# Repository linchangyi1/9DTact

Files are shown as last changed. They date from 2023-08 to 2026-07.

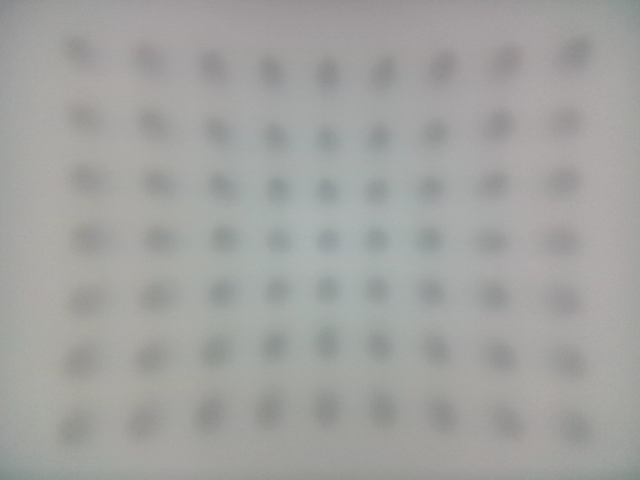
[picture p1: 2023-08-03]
shape_reconstruction/calibration/sensor_1/camera_calibration/sample.png

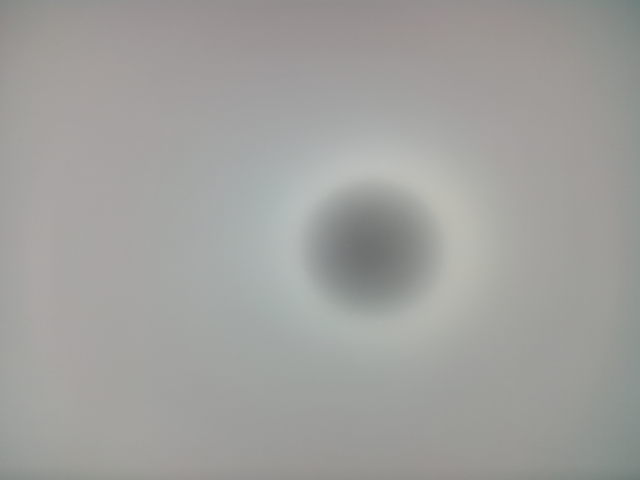
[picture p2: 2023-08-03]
shape_reconstruction/calibration/sensor_2/depth_calibration/sample.png

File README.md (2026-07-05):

# 9DTact
### Feel free to use this open-source project for commercial purposes!

# Table of contents
1. [Overview](#overview)
2. [Installation](#installation)
3. [3D Shape Reconstruction](#reconstruction)
   1. [Camera Calibration](#camera_calibration)
   2. [Sensor Calibration](#sensor_calibration)
   3. [Shape Reconstruction](#shape_reconstruction)
4. [6D Force Estimation](#estimation)
   1. [BOTA Driver](#bota)
   2. [Data Collection](#collection)
   3. [Data Processing](#processing)
   4. [Model Training](#training)
   5. [Force Estimation](#inference)
5. [Run in ROS](#ros)
   1. [Shape Reconstruction in ROS](#shape_ros)
   2. [Force Estimation in ROS](#force_ros)
   3. [Simultaneous Shape Reconstruction and Force Estimation (SSAF) in ROS](#shape_force)
6. [DTact Series Papers](#papers)

## Overview 
**This repository contains the code and the hardware source files for the paper:**



<b>9DTact: A Compact Vision-Based Tactile Sensor for Accurate 3D Shape Reconstruction and Generalizable 6D Force Estimation</b> <br>
[Changyi Lin](https://linchangyi1.github.io/),
[Han Zhang](https://doublehan07.github.io/),
Jikai Xu, Lei Wu, and
[Huazhe Xu](http://hxu.rocks/) <br>
RAL, 2023 <br>
[Website](https://linchangyi1.github.io/9DTact/) /
[Arxiv Paper](https://arxiv.org/abs/2308.14277) /
[Video Tutorial](https://www.youtube.com/watch?v=-oRtW398JDY) /
[Bom (CN)](https://docs.google.com/document/d/1d8c0Pbj_9otzWVxE94c6c-DW61ETBbJZIjVFKe4_OXI/edit?usp=sharing) /
[Production](https://e.tb.cn/h.hJlaI3aoyO30DGk?tk=K9Vm4iYdHwj)

## Installation 
#### Create a conda environment:
```bash
conda create -n 9dtact python=3.8
```
#### Install pytorch (choose the version that is compatible with your computer):
```bash
conda activate 9dtact
conda install pytorch torchvision torchaudio pytorch-cuda=11.8 -c pytorch -c nvidia
```
#### In this repository, install the other requirements:
```bash
pip install -e .
```

## 3D Shape Reconstruction 
For all the terminals used in this section, they are located in the **shape_reconstruction** directory and based on the **9dtact** conda environment:
```bash
cd shape_reconstruction
conda activate 9dtact
```

If you are using the **production** version of 9DTact, you do **not** need to calibrate the camera and sensor.
Please proceed directly to Step 3 (Shape Reconstruction).

### 1. Camera Calibration 
Before getting started, **adjust the camera focus** by rotating the lens until objects approximately 15 mm away appear clear.

Then, 3d print the [calibration board](9DTact_Design/fabrication/calibration_board.STL).<br>
Run:
```bash
python _1_Camera_Calibration.py
```
Just follow the printed instructions.

### 2. Sensor Calibration 
Firstly, prepare a ball with a radius of 4.0 mm.
(The radius of the ball depends on the thickness of the sensor surface.
4.0 mm is just a recommendation.)<br>
Then, run:
```bash
python _2_Sensor_Calibration.py
```
Just follow the printed instructions.

### 3. Shape Reconstruction 
```bash
python _3_Shape_Reconstruction.py
```
Press 'y' when the tactile image is stably captured, which will served as the reference image.

## 6D Force Estimation 
### 1. BOTA Driver 
**If you want to collect force data with a BOTA MiniONE Pro sensor, you need to:**<br>
Create a directory named 'bota_ws' as the ROS workspace, and install the [bota driver package](https://gitlab.com/botasys/bota_driver).

### 2. Data Collection 
#### At the first terminal, open the BOTA sensor:
```bash
cd ~/xxx/bota_ws # Modify 'xxx' to enter the workspace directory
source devel/setup.bash
roslaunch rokubimini_serial rokubimini_serial.launch
```
#### At the second terminal, run:
```bash
source ~/xxx/bota_ws/devel/setup.bash
cd data_collection
conda activate 9dtact
python collect_data.py
```
#### At the third terminal, open the 9DTact sensor:
```bash
cd shape-force-ros
conda activate 9dtact
python _1_Sensor_ros.py
```

### 3. Data Processing 
#### Open a terminal, normalize the wrench:
```bash
cd data_collection
conda activate 9dtact
python wrench_normalization.py  # remember to modify the object_num
```
#### At the same terminal, split the data by running:
```bash
python split_train_test.py
```
and also:
```bash
python split_train_test(objects).py
```

### 4. Model Training 
To train the model on the stadard training dataset, run:
```bash
cd force_estimation
python train.py --model_name="Densenet" --model_layer=169 --optimizer="ADAM" --lrs=False --image_type="RGB" --cuda_index=6 --resize_img=False --train_mode=True --test_object=False --mixed_image=True --pretrained=False --batch_size=64 --num_epoch=200 --learning_rate=5.0e-4 --weight_decay=0.0
```
You may also choose to use [Weights and Bias (wandb)](https://docs.wandb.ai/quickstart) by setting use_wandb as True,
which helps to track the training performance.

### 5. Force Estimation 
You need to specify a model saved in the 'saved_models' directory as an estimator,
by modifying the 'weights' parameters in the [force_config.yaml](force_estimation/force_config.yaml).<br>
After that, run:
```bash
cd force_estimation
python _1_Force_Estimation.py
```

## Run in ROS 
### 1. Shape Reconstruction in ROS 
#### At the first terminal, open the 9DTact sensor:
```bash
cd shape-force_ros
conda activate 9dtact
python _1_Sensor_ros.py
```
#### At the second terminal, run:
```bash
cd shape-force_ros
conda activate 9dtact
python _2_Shape_Reconstruction_ros.py
```

### 2. Force Estimation in ROS 
#### At the first terminal, open the 9DTact sensor:
```bash
cd shape-force_ros
conda activate 9dtact
python _1_Sensor_ros.py
```
#### At the second terminal, run:
```bash
cd shape-force_ros
conda activate 9dtact
python _3_Force_Estimation_ros.py
```
#### (Optional for visualization) At the third terminal, open the visualization window:
```bash
cd force_estimation
conda activate 9dtact
python force_visualizer.py
```
### 3. Simultaneous Shape Reconstruction and Force Estimation (SSAF) in ROS 
#### At the first terminal, open the force estimator:
```bash
cd shape-force_ros
conda activate 9dtact
python _3_Force_Estimation_ros.py
```
#### At the second terminal, run:
```bash
cd shape-force_ros
conda activate 9dtact
python _4_Shape_Force_ros.py
```
## DTact Series Papers 
- [DTact: A Vision-Based Tactile Sensor that Measures High-Resolution 3D Geometry Directly from Darkness](https://arxiv.org/abs/2209.13916), Lin et al., ICRA 2023
- [9DTact: A Compact Vision-Based Tactile Sensor for Accurate 3D Shape Reconstruction and Generalizable 6D Force Estimation](https://arxiv.org/abs/2308.14277), Lin et al., RAL 2023
- [Design and Evaluation of a Rapid Monolithic Manufacturing Technique for a Novel Vision-Based Tactile Sensor: C-Sight](https://www.mdpi.com/1424-8220/24/14/4603), Fan et al., MDPI Sensors 2024
- [DTactive: A Vision-Based Tactile Sensor with Active Surface](https://arxiv.org/abs/2410.08337), Xu et al., IROS 2025
- [VET: A Visual-Electronic Tactile System for Immersive Human-Machine Interaction](https://arxiv.org/pdf/2503.23440), Zhang et al., arxiv 2025
- [PP-Tac: Paper Picking Using Tactile Feedback in Dexterous Robotic Hands](https://arxiv.org/abs/2504.16649), Lin et al., RSS 2025
- [AllTact Fin Ray: A Compliant Robot Gripper with Omni-Directional Tactile Sensing](https://arxiv.org/pdf/2504.18064), Liang et al., arxiv 2025
- [SuperMag: Vision-based Tactile Data Guided High-resolution Tactile Shape Reconstruction for Magnetic Tactile Sensors](https://arxiv.org/pdf/2507.20002), Hou et al., IROS 2025
- [UTact: Underwater Vision-Based Tactile Sensor with Geometry Reconstruction and Contact Force Estimation](https://advanced.onlinelibrary.wiley.com/doi/pdfdirect/10.1002/adrr.202500091), Zhang et al., Advanced Robotics Research 2025
- [exUMI: Extensible Robot Teaching System with Action-aware Task-agnostic Tactile Representation](https://openreview.net/attachment?id=b86nyIOJWq&name=pdf), Xu et al., CoRL 2025
- [TacScope: A Miniaturized Vision-Based Tactile Sensor for Surgical Applications](https://advanced.onlinelibrary.wiley.com/doi/10.1002/adrr.202500117), Prince et al., Advanced Robotics Research 2025
- [Design and application of multimodal visual-tactile sensor for object information perception](https://www.sciencedirect.com/science/article/pii/S0924424726000804?via%3Dihub), Wang et al., Sensors and Actuators 2026
- [A Low-Cost Vision-Based Tactile Gripper with Pretraining Learning for Contact-Rich Manipulation](https://arxiv.org/pdf/2602.00514), Liu et al., arxiv 2026
- [SpikingTac: A Miniaturized Neuromorphic Visuotactile Sensor for High-Precision Dynamic Tactile Imprint Tracking](https://arxiv.org/pdf/2602.23654), Jiang et al., arxiv 2026
- [Heterogeneous Tactile Transformer](https://arxiv.org/pdf/2606.29948), Bi et al., arxiv 2026

## Reference
```
@inproceedings{lin2023dtact,
  title={Dtact: A vision-based tactile sensor that measures high-resolution 3d geometry directly from darkness},
  author={Lin, Changyi and Lin, Ziqi and Wang, Shaoxiong and Xu, Huazhe},
  booktitle={2023 IEEE International Conference on Robotics and Automation (ICRA)},
  pages={10359--10366},
  year={2023},
  organization={IEEE}
}
```
```
@article{lin20239dtact,
  title={9dtact: A compact vision-based tactile sensor for accurate 3d shape reconstruction and generalizable 6d force estimation},
  author={Lin, Changyi and Zhang, Han and Xu, Jikai and Wu, Lei and Xu, Huazhe},
  journal={IEEE Robotics and Automation Letters},
  volume={9},
  number={2},
  pages={923--930},
  year={2023},
  publisher={IEEE}
}
```

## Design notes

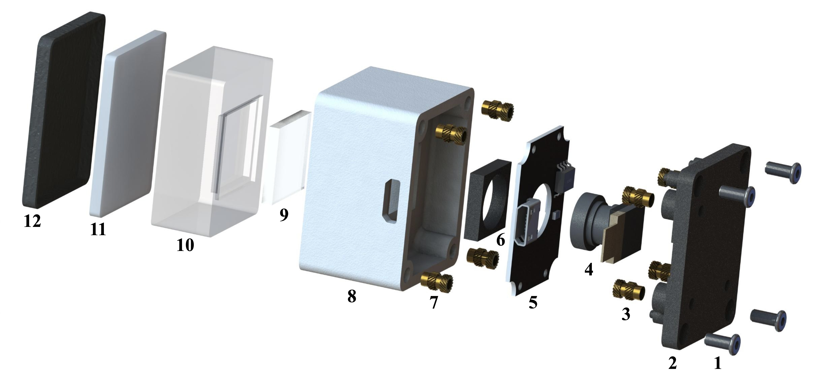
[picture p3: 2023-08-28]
source/design.jpeg

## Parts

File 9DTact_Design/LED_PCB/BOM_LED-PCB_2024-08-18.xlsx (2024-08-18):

No. | Quantity | Comment | Designator | Footprint | Value | Manufacturer Part | Manufacturer | Supplier Part | Supplier
1 | 8 | BZ-S2835BW9C1-02-3V-UV | LED1,LED2,LED3,LED4,LED5,LED6,LED7,LED8 | LED-SMD_L3.5-W2.8-FD-2835_WHITE |  | BZ-S2835BW9C1-02-3V-UV | baizou(百洲） | C2833052 | LCSC
2 | 1 | 20kΩ | R1 | R0805 | 20kΩ | RT0805CRE0720KL | YAGEO(国巨) | C706298 | LCSC
3 | 1 | CN5711 | U1 | SOIC-8_L5.0-W4.0-P1.27-LS6.0-BL-EP2.0 |  | CN5711 | CONSONANCE(上海如韵) | C35634 | LCSC
4 | 1 | MICRO-02-G4P1-A1T2 | USB3 | MICRO-USB-SMD_MICRO-02-GXPX-A1T2 |  | MICRO-02-G4P1-A1T2 | Yuandi(台湾元迪) | C2682525 | LCSC

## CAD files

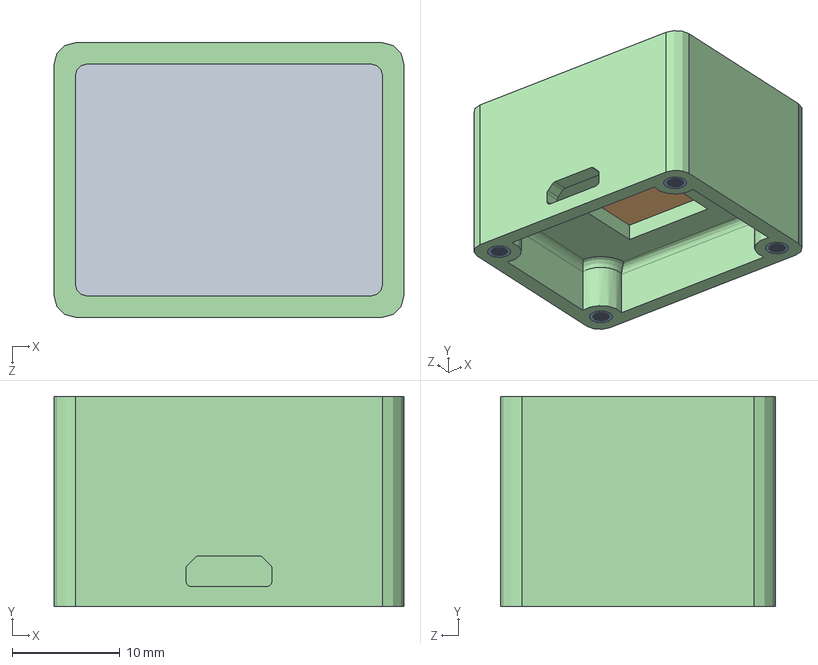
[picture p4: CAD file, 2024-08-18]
9DTact_Design/2_Diffusion_Module/2_Diffusion_Module.SLDASM
32.5 x 19.5 x 25.5 mm
sensor_shell
nut(2-3-5) x 4
acrylic_window
transparent_gel

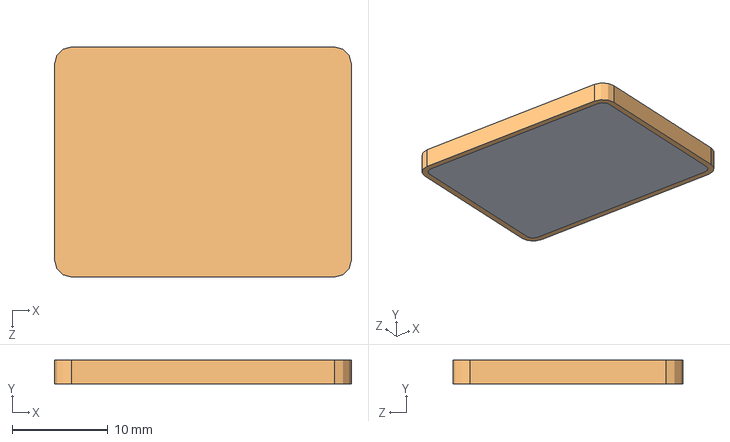
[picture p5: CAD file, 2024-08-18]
9DTact_Design/3_Contact_Module/3_Contact_Module.SLDASM
31.1 x 2.50 x 24.1 mm
translucent_gel
black_gel

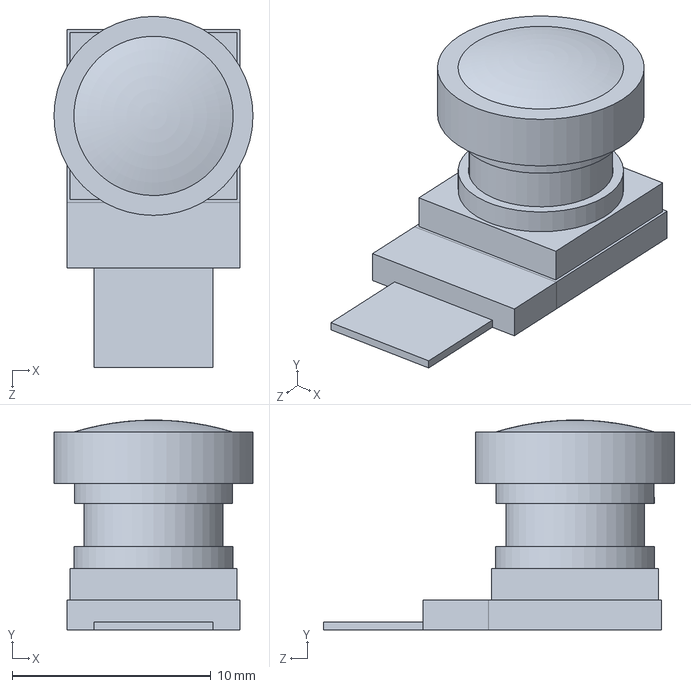
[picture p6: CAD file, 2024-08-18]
9DTact_Design/1_Perception_Module/camera(frank-s15-v1.0).SLDPRT
10.0 x 10.6 x 17.6 mm

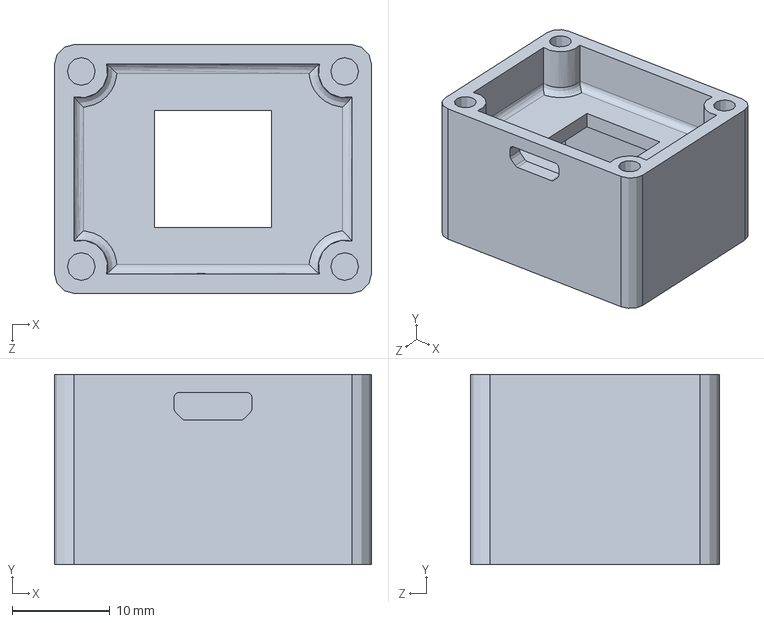
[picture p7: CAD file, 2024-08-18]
9DTact_Design/2_Diffusion_Module/sensor_shell.SLDPRT
32.5 x 19.5 x 25.5 mm

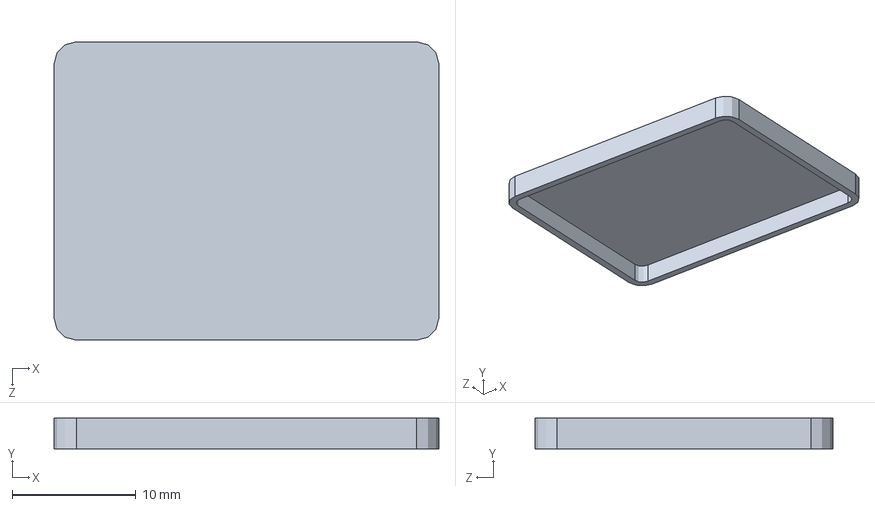
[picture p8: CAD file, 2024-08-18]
9DTact_Design/3_Contact_Module/black_gel.SLDPRT
31.1 x 2.50 x 24.1 mm

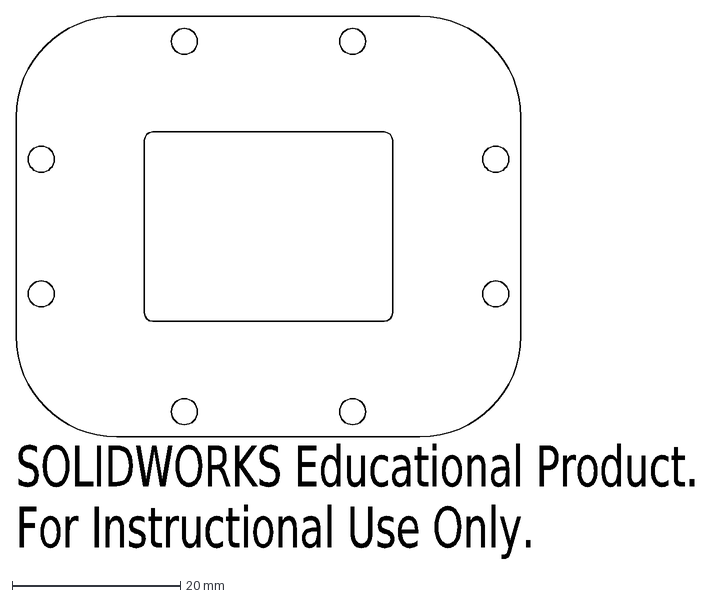
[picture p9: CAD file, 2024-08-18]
9DTact_Design/fabrication/mold_1_thickness_2.5mm.DXF
SOLIDWORKS Educational Product.
For Instructional Use Only.

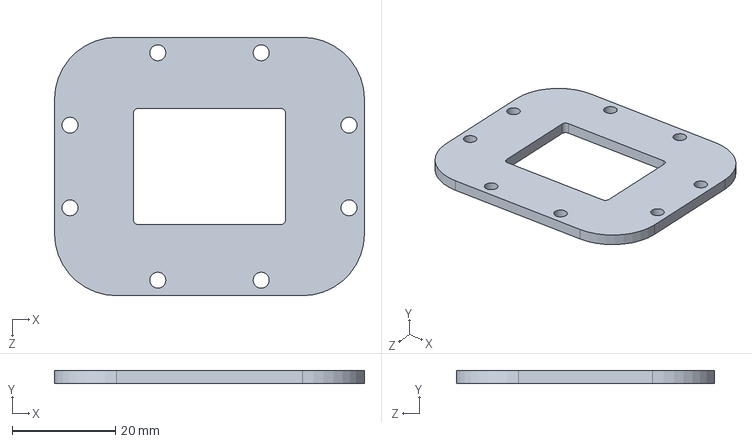
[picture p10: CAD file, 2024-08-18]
9DTact_Design/mold/mold_1.SLDPRT
60.0 x 2.50 x 50.0 mm

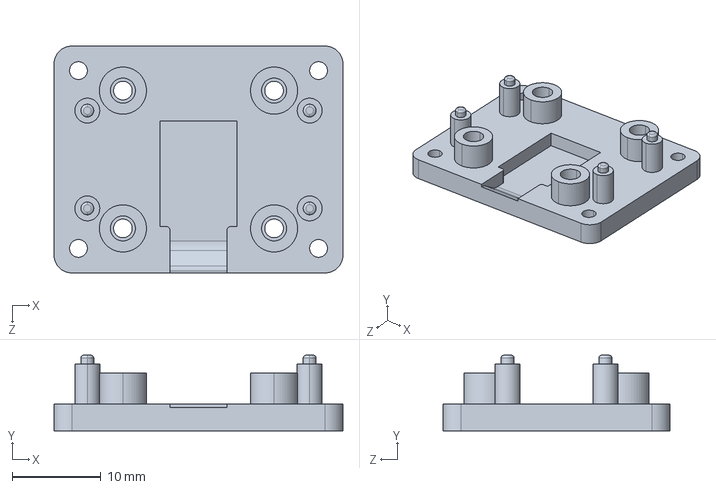
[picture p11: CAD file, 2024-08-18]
9DTact_Design/fabrication/sensor_base.STEP
32.5 x 8.50 x 25.5 mm

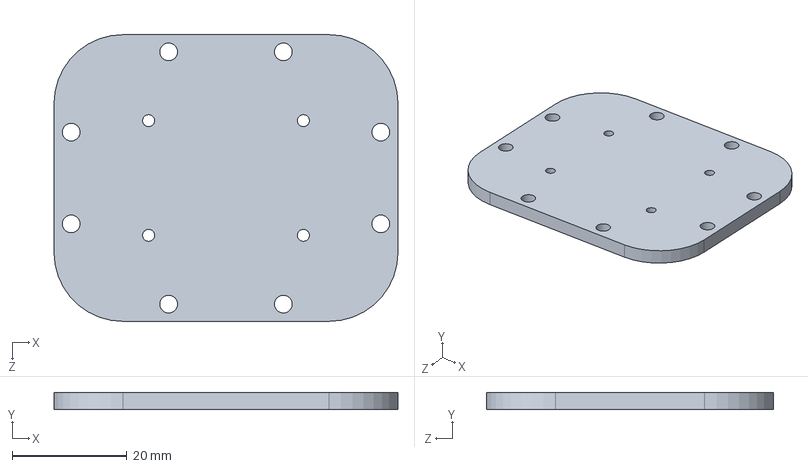
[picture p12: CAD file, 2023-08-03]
9DTact_Design/mold/mold_base.SLDPRT
60.0 x 3.00 x 50.0 mm

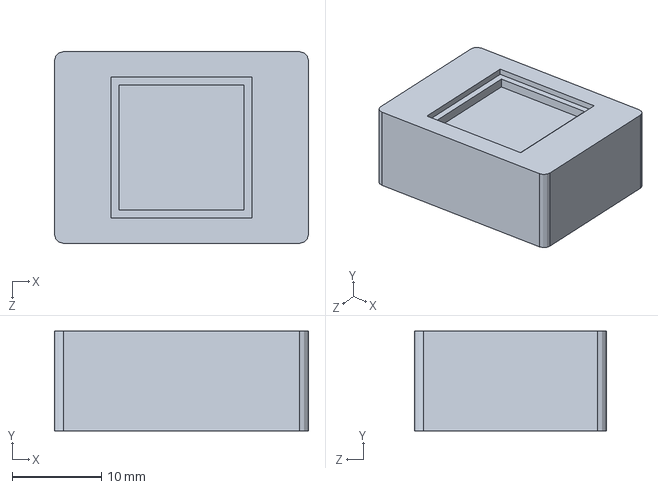
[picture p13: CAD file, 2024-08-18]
9DTact_Design/2_Diffusion_Module/transparent_gel.SLDPRT
28.5 x 11.2 x 21.5 mm

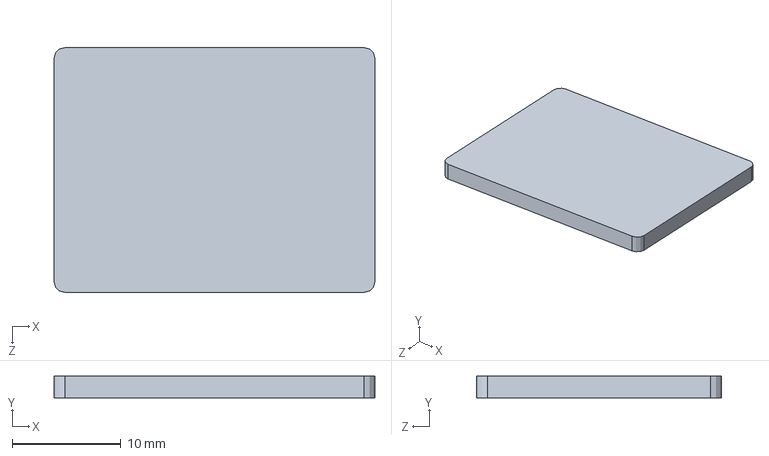
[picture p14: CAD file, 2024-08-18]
9DTact_Design/3_Contact_Module/translucent_gel.SLDPRT
29.5 x 2.00 x 22.5 mm

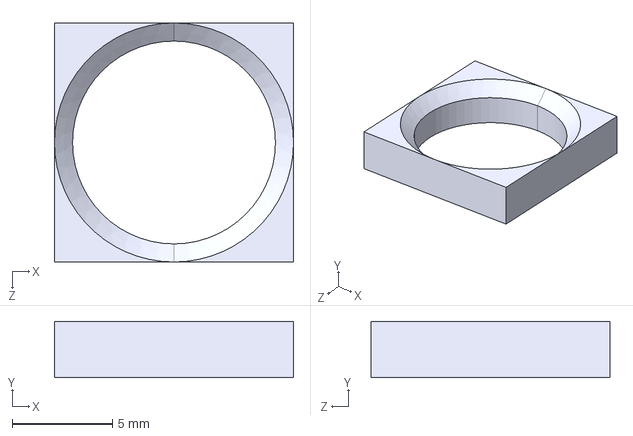
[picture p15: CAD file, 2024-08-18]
9DTact_Design/fabrication/isolation_ring.STEP
11.9 x 2.80 x 11.9 mm

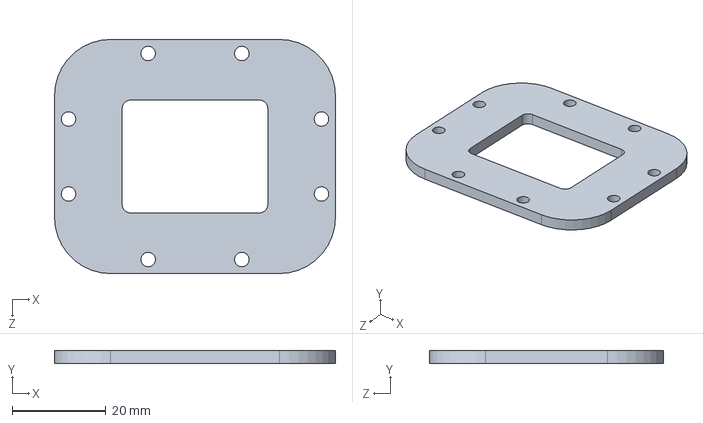
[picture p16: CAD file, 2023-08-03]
9DTact_Design/mold/mold_2.SLDPRT
60.0 x 2.80 x 50.0 mm

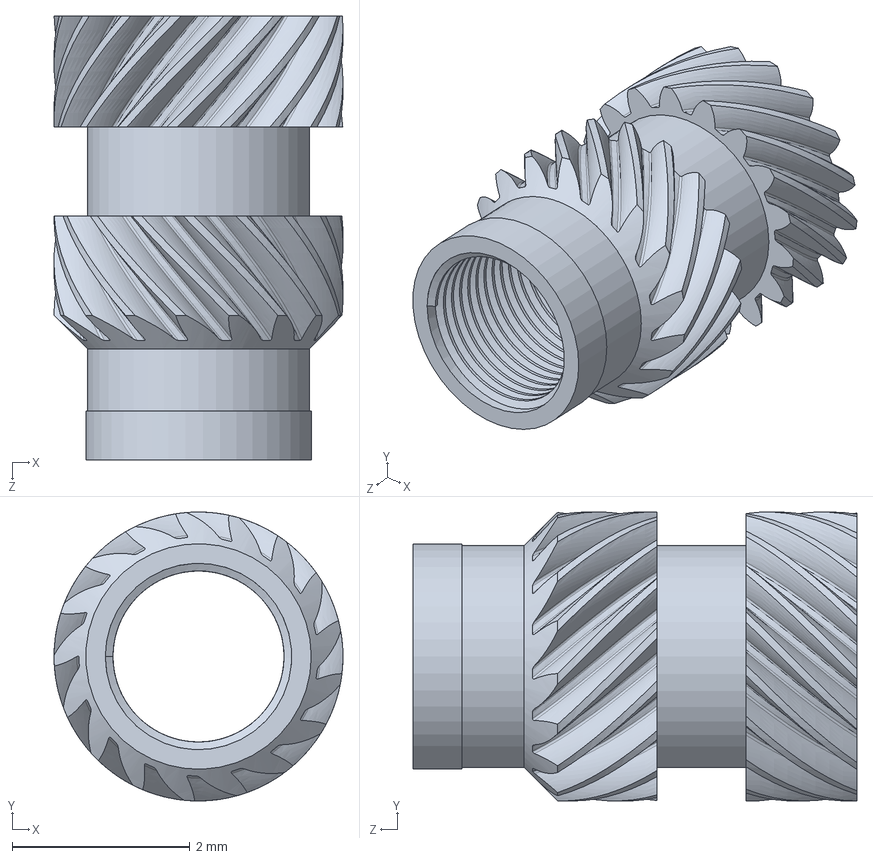
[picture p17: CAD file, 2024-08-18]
9DTact_Design/1_Perception_Module/nut(2-3-5).SLDPRT
3.26 x 3.25 x 5.00 mm

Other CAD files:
9DTact_Design/LED_PCB/LED_Model_from_JLC/led_board_combined.SLDASM
9DTact_Design/1_Perception_Module/sensor_base.SLDPRT
9DTact_Design/2_Diffusion_Module/acrylic_window.SLDPRT
9DTact_Design/fabrication/sensor_shell.STEP
9DTact_Design/1_Perception_Module/screw(M2-5).SLDPRT
9DTact_Design/2_Diffusion_Module/isolation_ring.SLDPRT
9DTact_Design/fabrication/calibration_board.SLDPRT
9DTact_Design/fabrication/calibration_board.STEP
9DTact_Design/fabrication/calibration_board.STL
9DTact_Design/fabrication/isolation_ring.STL
9DTact_Design/fabrication/mold_2_thickness_2.8mm.DXF
9DTact_Design/fabrication/mold_base_thickness_3.0mm.DXF
9DTact_Design/fabrication/sensor_base.STL
9DTact_Design/fabrication/sensor_shell.STL

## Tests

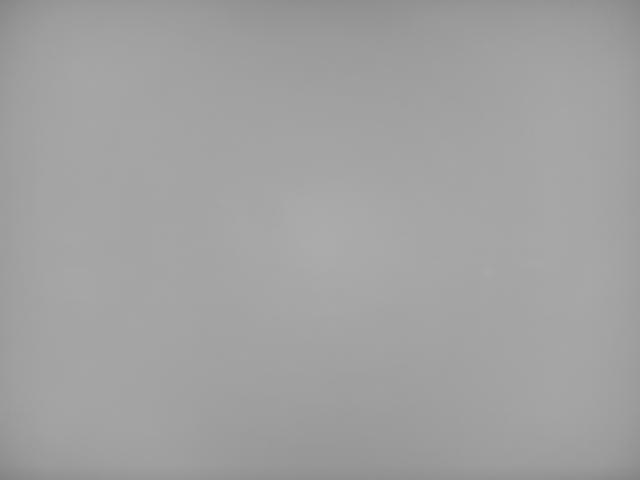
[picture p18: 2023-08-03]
shape_reconstruction/calibration/sensor_1/camera_calibration/ref_GRAY.png

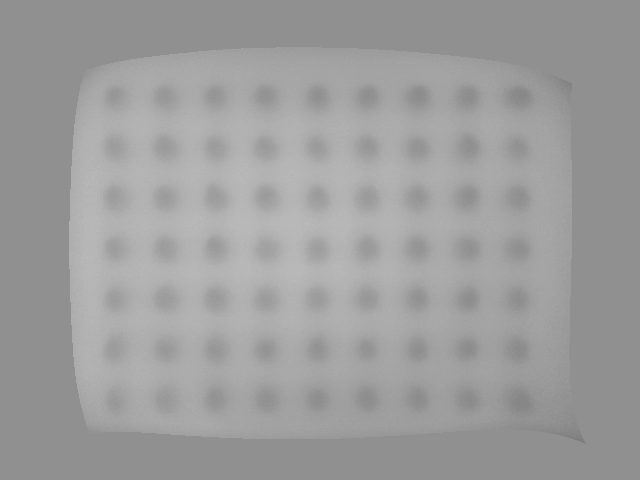
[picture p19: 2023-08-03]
shape_reconstruction/calibration/sensor_2/camera_calibration/sample_new.png

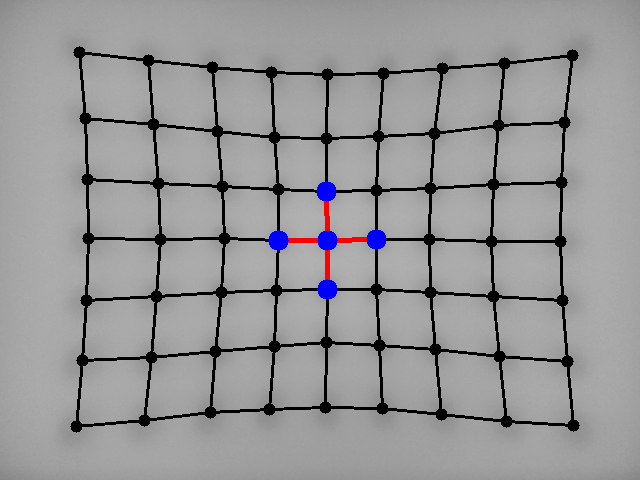
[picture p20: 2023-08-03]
shape_reconstruction/calibration/sensor_1/camera_calibration/sample_drawing.png

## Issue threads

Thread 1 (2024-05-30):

关于材料清单中硅胶型号和LED背光板PCB的购买问题

superfun77, 2024-05-30:
您好，我们在参考您提供的视频和材料清单制作项目时遇到了一些问题，希望能够得到您的帮助。

1.硅胶型号的国内采购问题
    我们在材料清单中看到硅胶的型号，但在国内的渠道上似乎没有找到标出同样型号的商店。能否提供透明和半透明硅胶的购买链接，确保我们可以购买到合适的产品？

2.黑色硅胶使用问题
    视频中展示的清单提到使用黑色硅胶，我们找到了相同型号的黑色硅胶，但发现价格不匹配。同时，在视频制作过程中，似乎是通过黑色色素而不是黑色硅胶来制作的。请问这种情况下，我们应该如何选择和使用材料？

3.LED背光板PCB的购买和制作问题
    关于LED背光板的PCB，我们不确定是否有现成的产品可以直接购买，还是需要自行制作。请问是否有相应的购买链接或制作方法可以提供？
    感谢您抽出时间阅读我们的问题，期待您的解答！

Closed 2024-06-29.

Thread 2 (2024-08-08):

Manufacturing Specs of LED PCB

abtabrizi, 2024-08-08:
Hi @linchangyi1, thank you for open-sourcing your sensor.
Can you kindly upload the JLCPCB manufacturing specifications used for the LED PCB?

The specs I am interested in are:
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

linchangyi1, 2024-08-08:
Hi, thanks for your interest in 9DTact. I have also open source the PCB source file in https://github.com/linchangyi1/9DTact/tree/640c35e9b5cf870f2d5c2a9d42e26e03bbcbaead/9DTact_Design/LED_PCB

Could you please check the files and see whether more information is still needed.

abtabrizi, 2024-08-08:
> Could you please check the files and see whether more information is still needed.

I did check the files and the manufacturing specs are missing.
Can you kindly provide a PDF containing the specs listed above? They are necessary for placing PCB orders on JLCPBC.

Also, for the LEDs, the supplier part # should be updated to C2833055 in the BOM:
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

Closed 2024-08-09.

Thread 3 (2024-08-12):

Body Collision in SW Model

abtabrizi, 2024-08-12:
Hi @linchangyi1,
I was looking at the `1_Perception_Module.SLDASM` model provided an noticed that a chip on the `led_board.SLDPRT` (Part # CN5711) and the sensor base are colliding:

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

Is this just an error in the SW model?
Please clarify.

linchangyi1, 2024-08-18:
Hi @abtabrizi, I checked the real board and it should be fine if you have fabricated the PCB:
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

Even though, I have placed the chip closer to the center, and it now looks like this:
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

abtabrizi, 2024-08-18:
hi @linchangyi1, in the updated LED models the thickness of the board has changed to `1.6 mm`. Previously it was `0.8 mm`. Please clarify what is the actual thickness of the PCB.

linchangyi1, 2024-08-18:
The JLC software can only export PCB model with the thickness of 1.6mm. While for fabrication, please choose 0.8mm. In addition, I will update the LED model to be 0.8mm thick in solidworks with some tricks.

Closed 2024-08-18.

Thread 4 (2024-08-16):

Regarding Dimension of Molds

abtabrizi, 2024-08-16:
hi @linchangyi1,

I noticed that the inner frame size of the molds are identical. Please refer to the following files on the repo:
**First Mold**: `mold_1.SLDPRT`
**Second Mold:** `mold_2.SLDPRT`

Assuming that the **First Mold is used for the translucent gel**, and the **Second Mold for the Black gel**, the inner frame sizes cannot be identical because the four sides of the translucent gel layer will not get covered by black gel. For your reference I have attached snapshots of the dimensions.

**Fig. 1** SW model of First Mold
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

**Fig. 2** SW model of `translucent_gel.SLDPRT`
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

**Fig. 3** SW model of Second Mold
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

**Fig. 4** SW model of `black_gel.SLDPRT`
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

linchangyi1, 2024-08-18:
Hi @abtabrizi, thanks a lot for reporting the bug. I just checked the solidworks files and found that I forgot to suppress the cutting feature for mold_2. I have modified it and uploaded the DXF files in the "fabrication" directory.

abtabrizi, 2024-08-19:
@linchangyi1 Can you please upload the DXF file for the acrylic mold removal tool?

linchangyi1, 2024-08-19:
I didn't find it on my new computer. You can just use any board that is a bit smaller than the inner size of mold_1.

Closed 2024-08-18.

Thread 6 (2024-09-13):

Thickness Tolerance of Acrylics

abtabrizi, 2024-09-13:
Hi @linchangyi1,

I am interested to know the actual measurement for the thickness of the acrylic molds.
Are the 2.5mm and 2.8mm numbers reported exact measurements or there is a tolerance associated with them (i.e. 2.5 is actually 2.3 when measured with a caliper)?

linchangyi1, 2024-09-13:
Hi @abtabrizi,

The thickness reported in the paper is an ideal value. Small variations in thickness are acceptable, as long as mold_2 remains thicker than mold_1. However, if the manufactured mold's thickness significantly deviates from the CAD model, you may need to adjust the height of the calibration part according to the new thickness.

abtabrizi, 2024-09-13:
That makes sense. Does slight variations in the thickness with respect to their ideal values (i.e. 0.3mm difference) impact the results when using your pre-trained model?

linchangyi1, 2024-09-13:
Yes, that would likely degrade performance. Although the gel layers of your sensor have been ideally manufactured, it's difficult to guarantee good performances if you directly use the open-sourced model to predict the force, because there are various factors that would cause the new sensor's tactile images to differ from the one used for collecting data. Therefore, it's recommended to use the open-source model as pre-trained weights, and collect data from your own sensor to fine-tune the model for better results.

abtabrizi, 2024-09-13:
Ideally how many images should be collected for fine-tuning the model using the pre-trained weights?

linchangyi1, 2024-09-15:
No sure about this as I have never tried.

abtabrizi, 2024-09-16:
Hi, onto another topic, I was wondering what gauge needle (light blue color) was being used in minute 3 of the tutorial (gluing acrylic window to nylon shell)?
I tried it with 25 gauge needle but it was very difficult to sneak in the glue between the acrylic and the nylon wall, there is hardly any gap. The glue would just spill out onto the surface of the window and the sensor shell.

linchangyi1, 2024-09-21:
I used 23 gauge needles. This step is almost the most difficult part of the entire process. You need to be very careful in controlling the amount of glue injected.

abtabrizi, 2024-09-21:
That makes sense. I noticed strange artifacts/particles inside the material of the acrylic window (shown in the images below). There is no dust on the surface of the window because I used the blue stickers to remove dust. The particles become visually apparent when you hold the window under light. Did you notice something like this? Will this be problematic? (I have windows from 2 different manufacturers and both are like this).

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

linchangyi1, 2024-09-21:
I suppose that it's scratch on the surface instead of particles inside the material. I also met this problem and I asked the manufacturer not to remove the film covered on the acrylic board when they cut it. This must be issued for good sensing of the camera.

abtabrizi, 2024-09-21:
The film stayed on during laser cutting. Does it matter if the thickness of the window is 0.5mm off the ideal value? The reason I'm asking is because I was able to find windows that had less surface imperfections but the thickness is around 1.5mm.

linchangyi1, 2024-09-21:
If the film stayed during cutting, it should be almost transparent after you take it off. It should be ok to have that thickness as long as you glue it very well.

Closed 2024-09-21.

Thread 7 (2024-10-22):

Camera Calibration Error: IndexError: index 13 is out of bounds for axis 0 with size 13... Error with code? or Process?

f5ces27er5c767s, 2024-10-22:
Hi there @linchangyi1 ,

Thank you so kindly for providing the code! What a wonderful project :)

We managed to get the sensor hardware working and are now at the camera calibration step. Getting the raw image saved was okay but in the next step where I was asked to push the calibration board on the sensor and then press "y" I get this bug. Do you happen to know how to resolve this?

This was my terminal line and error:
```

Legion-Pro-5-16IRX8:~/9DTact/shape_reconstruction$ python _1_Camera_Calibration.py
------Camera is open--------
DON'T touch the sensor surface!!!!!
Please press "y" to save the reference image!
Reference image saved!
Please press the calibration board on the sensor and press "y" to save the sample image!
yyTraceback (most recent call last):
  File "_1_Camera_Calibration.py", line 180, in <module>
    cc.run()
  File "_1_Camera_Calibration.py", line 42, in run
    self.calibrate_image(ref, sample)
  File "_1_Camera_Calibration.py", line 92, in calibrate_image
    (all_point[i*self.col_points+j + 1][1], all_point[i*self.col_points+j + 1][0]), command_color,
IndexError: index 13 is out of bounds for axis 0 with size 13

```

Is there an error in the code? Am I supposed to push down really hard or do I only need to do it slightly? Do I need to just push until I see all dots of the calibration board on the sensor?

Thank you kindly @linchangyi1 , please let me know if you resolve this! I also attach an image of my process.

linchangyi1, 2024-10-22:
Hi @f5ces27er5c767s , I think you probably need to push it down really hard for clear imprints. Btw, have you attached the image? I didn't see that

f5ces27er5c767s, 2024-10-24:
Hi @linchangyi1 Thank you for replying back to me so quickly, so sorry for the late reply it got busy here haha.

The image of the calibration board for this camera calibration step is as follows:

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

I tried your approach of pushing it down really hard and I get the same errors, now though with differing IndexError (i.e. the number of index out of bounds is different each time). For 2-3 really hard presses I get the following output:
```

(9dtact) Legion-Pro-5-16IRX8:~/9DTact/shape_reconstruction$ python _1_Camera_Calibration.py
------Camera is open--------
DON'T touch the sensor surface!!!!!
Please press "y" to save the reference image!
Reference image saved!
Please press the calibration board on the sensor and press "y" to save the sample image!
Traceback (most recent call last):
  File "_1_Camera_Calibration.py", line 180, in <module>
    cc.run()
  File "_1_Camera_Calibration.py", line 42, in run
    self.calibrate_image(ref, sample)
  File "_1_Camera_Calibration.py", line 92, in calibrate_image
    (all_point[i*self.col_points+j + 1][1], all_point[i*self.col_points+j + 1][0]), command_color,
IndexError: index 46 is out of bounds for axis 0 with size 46
(9dtact) Legion-Pro-5-16IRX8:~/9DTact/shape_reconstruction$ python _1_Camera_Calibration.py
------Camera is open--------
DON'T touch the sensor surface!!!!!
Please press "y" to save the reference image!
Reference image saved!
Please press the calibration board on the sensor and press "y" to save the sample image!
Traceback (most recent call last):
  File "_1_Camera_Calibration.py", line 180, in <module>
    cc.run()
  File "_1_Camera_Calibration.py", line 42, in run
    self.calibrate_image(ref, sample)
  File "_1_Camera_Calibration.py", line 92, in calibrate_image
    (all_point[i*self.col_points+j + 1][1], all_point[i*self.col_points+j + 1][0]), command_color,
IndexError: index 50 is out of bounds for axis 0 with size 50
(9dtact) Legion-Pro-5-16IRX8:~/9DTact/shape_reconstruction$ python _1_Camera_Calibration.py
------Camera is open--------
DON'T touch the sensor surface!!!!!
Please press "y" to save the reference image!
Reference image saved!
Please press the calibration board on the sensor and press "y" to save the sample image!
Traceback (most recent call last):
  File "_1_Camera_Calibration.py", line 180, in <module>
    cc.run()
  File "_1_Camera_Calibration.py", line 42, in run
    self.calibrate_image(ref, sample)
  File "_1_Camera_Calibration.py", line 92, in calibrate_image
    (all_point[i*self.col_points+j + 1][1], all_point[i*self.col_points+j + 1][0]), command_color,
IndexError: index 48 is out of bounds for axis 0 with size 48
(9dtact) Legion-Pro-5-16IRX8:~/9DTact/shape_reconstruction$
```

Any suggestions? I am pressing it so hard that the calibration  board now has made marks on the top gel. I don't think it's my sensor, do you happen to know how we can resolve this? :)

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

Thank you! @linchangyi1

linchangyi1, 2024-10-24:
Hi @f5ces27er5c767s ,

Actually you tactile image for calibration is not clear enough although you have pressed the board very hard. I think this is because you haven't adjust the camera focus very well. As for a good calibration image, refer to the tactile image for calibration in the paper.

The marks on the top gel should disappear soon after you remove your calibration board. If you are facing that problem, you may need to check whether you choose the same material as that used for the original 9DTact.

f5ces27er5c767s, 2024-10-24:
Hi @linchangyi1 by "adjusting the camera focus" apologies for the simple question, but do you have any recommendations as to how to do this? :)

I am not quite sure how to adjust the camera focus, do you mean I need to open the camera up and fix the lens? Or is there a program/file you know of that could fix this camera focus?

Thank you kindly for your message replies, they are really helping! @linchangyi1 :)

abtabrizi, 2024-10-24:
hi @linchangyi1, with regards to objects leaving imprints on the black gel, I faced the same issue. I used same the materials listed in the paper, however, for the black pigment I used [Smooth-on Black Slic Pig](https://www.smooth-on.com/products/silc-pig/) as opposed to the one you recommended.
> The marks on the top gel should disappear soon after you remove your calibration board. If you are facing that problem, you may need to check whether you choose the same material as that used for the original 9DTact.

linchangyi1, 2024-10-24:
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

Hi @f5ces27er5c767s, yes you need to rotate the lens of the camera until you see a clear tactile image.

linchangyi1, 2024-10-24:
> hi @linchangyi1, with regards to objects leaving imprints on the black gel, I faced the same issue. I used same the materials listed in the paper, however, for the black pigment I used [Smooth-on Black Slic Pig](https://www.smooth-on.com/products/silc-pig/) as opposed to the one you recommended.
>
> > The marks on the top gel should disappear soon after you remove your calibration board. If you are facing that problem, you may need to check whether you choose the same material as that used for the original 9DTact.

Hi @abtabrizi, I am not sure if it's caused by the pigment you chose. One point I could recommend is to ensure that the gel is fully "dry" after curing.  I also suspect that if your printer has low accuracy or if the calibration board has sharp edges, it could be contributing to the problem.

abtabrizi, 2024-10-24:
@linchangyi1 you are correct, I printed the board using PLA on an old printer and the dots on the board were sharp. I will try nylon printing.
> I also suspect that if your printer has low accuracy or if the calibration board has sharp edges, it could be contributing to the problem.

f5ces27er5c767s, 2024-10-25:
Hi @linchangyi1 thank you for messaging, we adjusted the focus of the camera and fixed it but in running the python Camera Calibration we still get the same issue. I tried it various times now with 1) fixed camera focus and 2) making sure to press hard on the sensor, the outputs I get still result in some IndexError:
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
f5ces27er5c767s, 2024-10-25:
@linchangyi1 This is my images with the camera focus fixed:

left is without calibration board, **right with calibration board pressed really hard too**:

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

linchangyi1, 2024-10-25:
Hi @f5ces27er5c767s,

The total number of point candidates should be 7 * 9 = 63. The issue arises because fewer than 63 points are being detected. One possible reason is that the imprints near the edges of your tactile image aren’t clear enough—please refer to the calibration image in the paper. Additionally, please double-check the camera’s focus and the printed calibration board.

f5ces27er5c767s, 2024-11-01:
Hi @linchangyi1 thank you kindly, we managed to finally get the 63 points recognized and detected by being more careful with the gel layer dimensions and also found a darker lower light room helped. We wanted to know if the images/processes we went through below are what we should and you expect :)

Below went through 1. camera calibration, 2. sensor calibration with a 4mm radius ball, 3. shape reconstruction:

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

Specifically in the end of the camera calibration process it just outputs: [234, 315, 0.055848595538478304]

The questions I want to ask are as follows:

1. what is the next step? We did all calibration steps now. Does finishing the calibration save all these results to some config for the model and then we can just automatically run the force estimation? What are the steps/commands for that?
2. Is the shape reconstruction image okay? Does this just output the shape, which in this case here is just the circular ball?
3. what exactly are the numbers in [234, 315, 0.055848595538478304]? are they saved?

Thank you kindly @linchangyi1 I appreciate your time, efforts and help very much :) You are awesome.

linchangyi1, 2024-11-04:
1. The calibration steps are just for shape reconstruction. For force estimation, you probably need to collect more data with your own sensors and use the released checkpoint as a pre-trained model.
2. I think they are ok based on your calibration image. You can get the height map and point clouds, please read the code for more details.
3. It's position_scale and is saved. Please read the code for more details.

linchangyi1, 2024-11-04:
@f5ces27er5c767s  It would be helpful if you can share how you finally got the clear tactile image. That definitely helps more people to reproduce 9DTact.

Closed 2024-11-04.

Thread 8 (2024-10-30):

Manufacturing Black Gel Layer

abtabrizi, 2024-10-30:
hi @linchangyi1, when manufacturing the black gel layer, do I fill up the entire space between the mold and the translucent gel with black gel? by the 'space' I'm referring to the 4 sides highlighted below. The spaces are 0.8 and 0.95mm thick.

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

linchangyi1, 2024-10-31:
Yes, you need to fill it.

Closed 2024-10-31.

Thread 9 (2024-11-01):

What exactly are the units for the force output on the test_image.png when running the force estimator?

f5ces27er5c767s, 2024-11-01:
Hi @linchangyi1 thank you for your strong guidance and help,

I also wanted to start a new github thread and ask about this output we got when testing the force estimate when running estimator.py:

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

Please just focus in on the force estimate output: [0.5228931  0.47465006 0.73858875 0.46580032 0.53931546 0.4671362]

I wanted to ask, what units is each element in? Is it Newtons (N) or milli-Newtons? and what about the torques?

Before the 3-step calibration process we tried testing the model accuracy on a single image whose associated force exertion we know (from our own ground-truth load cell) but the results were greatly different, and maybe it is because the units are not the same. Is the 3-step camera calibration process essential for accurate force-estimate?

Thank you @linchangyi1 kindly for all your help! We are excited to get this sensorr working!!

linchangyi1, 2024-11-04:
The output is the 6d normalized force estimation which is in the range of [0, 1]. Please check 'wrench_range' in https://github.com/linchangyi1/9DTact/blob/main/data_collection/wrench_normalization.py for real scale.
The calibration steps are just for shape reconstruction. Please read the paper and the code for more details.

f5ces27er5c767s, 2024-11-05:
Hi @linchangyi1 thanks for messaging and replying, I see about the normalized force estimation output. I modified the code below so as to also output the unnormalized real scale values of the force. I am having trouble understanding why on a test image with no force applied to it at all, the reading in Fz gives a nonzero value, could you help us with this? :)

My modified estimator.py is:

```
import os
import sys

sys.path.append(os.path.dirname(os.path.abspath(__file__)) + '/../')
import yaml
import torch
import numpy as np
np.set_printoptions(suppress=True)
import argparse
from model import *
import cv2

class Estimator:
    def __init__(self, cfg):
        parser = argparse.ArgumentParser()
        parser.add_argument("--model_name", default=None, type=str)
        parser.add_argument("--model_layer", default=None, type=str)
        parser.add_argument("--cuda_index", default=None, type=int)
        args = parser.parse_args()

        # parameters
        model_name = args.model_name if args.model_name is not None else cfg['model_list'][cfg['model_choice']][0]
        model_layer = args.model_layer if args.model_name is not None else cfg['model_list'][cfg['model_choice']][1]
        model_type = model_name + '-' + str(model_layer)
        cuda_index = args.cuda_index if args.cuda_index is not None else cfg['cuda_index']

        # model configuration
        self.device = torch.device(f"cuda:{cuda_index}" if torch.cuda.is_available() else "cpu")
        if model_name == 'Resnet':
            self.model = Resnet(layer=int(model_layer), pretrained=False).to(self.device)
        elif model_name == 'Densenet':
            self.model = Densenet(layer=int(model_layer), pretrained=False).to(self.device)

        self.save_dir = cfg['save_dir'] + '/' + model_type + str(cfg['weights'][cfg['model_choice']][0])
        weights_path = self.save_dir + '/epoch_' + str(cfg['weights'][cfg['model_choice']][1]) + '.pt'
        self.model.load_state_dict(torch.load(weights_path, map_location=self.device))
        self.model.eval()
        # inferring the first image takes more time than the latter images, so we pass it
        with torch.no_grad():
            two_img = np.ones((2, 3, cfg['img_size'][0], cfg['img_size'][1]))
            representation = torch.from_numpy(two_img).float().to(self.device)
            self.model(representation)
        print("Ready to predict the 6D force!")

        # wrench range setup for un-normalization
        self.wrench_range = np.array([[-3, 3], [-3, 3], [-12, 0], [-0.2, 0.2], [-0.2, 0.2], [-0.05, 0.05]])
        self.min_wrench = self.wrench_range[:, 0]
        self.max_wrench = self.wrench_range[:, 1]
        self.wrench_span = self.max_wrench - self.min_wrench

    def predict_force(self, representation):
        representation = representation.transpose([2, 0, 1])
        input_batch = 2
        if input_batch == 2:
            two_img = np.array([representation, representation])
            representation = torch.from_numpy(two_img).float().to(self.device)
            with torch.no_grad():
                force = self.model(representation)
                force[force < 0] = 0
                force[force > 1] = 1
                force = force.cpu().numpy()[0]
        else:
            representation = torch.from_numpy(np.array(representation)).float().to(self.device)
            with torch.no_grad():
                force = self.model(representation)
                force[force < 0] = 0
                force[force > 1] = 1
                force = force.cpu().numpy()

        # Unnormalize to get the real-world force values
        real_force = force * self.wrench_span + self.min_wrench

        return force, real_force

if __name__ == '__main__':
    f = open("force_config.yaml", 'r+', encoding='utf-8')
    config = yaml.load(f, Loader=yaml.FullLoader)
    estimator = Estimator(config)
    image = cv2.imread('test.png')
    input_image = np.zeros_like(image)
    input_image[::, ::, 0] = cv2.cvtColor(image, cv2.COLOR_BGR2GRAY)
    normalized_force, real_force = estimator.predict_force(input_image)
    print("Normalized 6D force output:", normalized_force)
    print("Real 6D force output (unnormalized):", real_force)

```

Also on a test image with no force applied, shouldn't the 6D vector of Fx,Fy,Fz,Tx,Ty,Tz all be zero?

This is what I got on a test image with no force applied after camera calibration, sensor calibration and sensor calibration. I also made sure we are using the DenseNet-169 pre-trained values you mentioned in my previous inquiry:

Force estimate on test image with no force applied for sure:

```
use Densenet-169
Ready to predict the 6D force!
Normalized 6D force output: [0.5182026  0.47572857 0.65638834 0.4747542  0.544809   0.46920186]
Real 6D force output (unnormalized): [ 0.10921562 -0.14562857 -4.12333989 -0.01009831  0.01792359 -0.00307981]

```

Why Fz=-4.12333989? Why any of these values nonzero? Shouldn't they all be zero?

This was my test image which no force is applied:

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

We are so close to getting this working, thank you for your continued help and support @linchangyi1 ! We appreciate you very much :)

linchangyi1, 2024-11-05:
Hi @f5ces27er5c767s, the pre-trained model will output non-zero values because it was trained on the dataset collected from my sensor. That's why you need to collect data from your sensor for fine-tuning the model.

f5ces27er5c767s, 2024-11-05:
@linchangyi1 Ok thanks, so I should expect though those values to be zero though if I collect data from my sensor?

linchangyi1, 2024-11-06:
If you retrain the model, the output is expected to be zeros, but actually it will not be exactly zero because of the small estimation error.

Closed 2024-11-04.

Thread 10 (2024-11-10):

Cost of the BOTA minione Sensor for F/T for 6D F/T Estimation?

f5ces27er5c767s, 2024-11-10:
Hi @linchangyi1 I have been looking everywhere for the cost/price of the BOTA minione Sensor used in the paper, did you order it from the main website or from some third party vendor?

We might need it to further retune our model but even contacting them we are getting no reply.

Apologies, we know this might not be the right place to ask but it is worth trying because we want to get your work running for our research application :) Thank you!

linchangyi1, 2024-11-10:
Hi, I did this project in China and purchased it from a third-party vendor. If you are also based in China, you can email me for the contact information.

abtabrizi, 2024-11-21:
hi @linchangyi1, looking at the BOTA sensors, did you use the Serial or USB variation of the MiniONE pro?

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

from your experience, was the sensor easy to setup and work with? did it require any signal conditioners/amplifier boards + power supplies to operate the sensor? I'm asking this because most 6-axis F/T sensors I have seen required additional modules/boards aside from the sensor itself, for example, the ATI 6-axis sensor we have in our lab requires the following setup:

<a href="url">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</a>

lastly, should I be able to use the MiniONE non-pro USB version for data collection? assuming that I would have to tweak the codes provided on your repo.

linchangyi1, 2024-11-22:
I used the USB one. It's easy to set up it, just requiring the force sensor itself.

Closed 2024-11-17.

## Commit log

2023-08-28 add open source.
    [1_Perception_Module.SLDASM, 2_Diffusion_Module.SLDASM, 3_Contact_Module.SLDASM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]
2024-08-18 update mold_1 and led_board
    [2_Diffusion_Module.SLDASM, 3_Contact_Module.SLDASM, acrylic_window.SLDPRT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]
2024-08-18 update led_board and mold_1
    [2_Diffusion_Module.SLDASM, 3_Contact_Module.SLDASM, BOM_LED-PCB_2024-08-18.xlsx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]
2024-08-18 Revert "update led_board and mold_1"
    This reverts commit 6da3d4b39e751cd5fe2d85149e767f6401635d42.
    [2_Diffusion_Module.SLDASM, 3_Contact_Module.SLDASM, BOM_LED-PCB_2024-08-18.xlsx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]
2024-08-18 add open source
    [2_Diffusion_Module.SLDASM, 3_Contact_Module.SLDASM, BOM_LED-PCB_2024-08-18.xlsx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]
2024-08-18 update open source.
    [2_Diffusion_Module.SLDASM, 3_Contact_Module.SLDASM, BOM_LED-PCB_2024-08-18.xlsx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]
2026-02-01 Add reference for multimodal visual-tactile sensor
    Added a new reference for a multimodal visual-tactile sensor.
2026-02-04 Add reference for low-cost vision-based tactile gripper
    Added a new reference for a low-cost vision-based tactile gripper.
2026-03-04 Add new reference for SpikingTac sensor
